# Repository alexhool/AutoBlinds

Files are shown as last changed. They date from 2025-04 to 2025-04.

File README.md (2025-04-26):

# AutoBlinds
### ECE 4180 - Embedded Systems Project

---

## Project Overview

This project automates the opening and closing of roller blinds operated by a beaded chain, enhancing user convenience
and accessibility. The system can be retrofitted to most existing chain operated blinds. It utilizes an ESP32-C6
microcontroller to control a DC motor to open, close, or move the blinds to specific positions. Users can interact with
the system through several methods: **tactile switches** for manual operation, **time-of-flight (ToF) sensor** for
proximity control, and a **web interface** for remote activation and configuring daily activation schedules. The system
operates using a finite state machine with several distinct modes:

* **Toggle Mode:** Default operation mode where pressing the Open/Close buttons or proximity detection via the ToF
sensor move the blinds to their configured positions.

* **Manual Mode:** Activated by a pressing the Mode button, allows for precise position control by holding the
Open/Close buttons. The system automatically returns to Toggle Mode after a set timeout.

* **Configuration Mode:** Activated by holding the Mode button, allows the user to set the fully open and closed
position limits into non-volatile memory by holding the Open/Close buttons. The system automatically returns to Toggle
Mode after a set timeout.

---

## System Components

* **Microcontroller (ESP32-C6-DevKitC-1):** The central processing unit, executing the main control loop and
state machine logic. It manages peripherals via GPIO and I2C, handles networking tasks (Wi-Fi connection, Network Time
Protocol (NTP) synchronization, web interface), reads the encoder with its internal Pulse Counter (PCNT) module, and
controls the motor driver.

* **DC Motor w/ Encoder (JGY-370-EN):** A 158:1 geared DC motor that drives the physical movement of the blinds via the
beaded chain. Its integrated quadrature encoder provides rotational feedback for precise position tracking.
    + **3D-Printed Sprocket:** Mechanically couples the motor shaft to the beaded chain with the correct pitch and
        diameter. Model files available in `assets/`.<br/><br/>
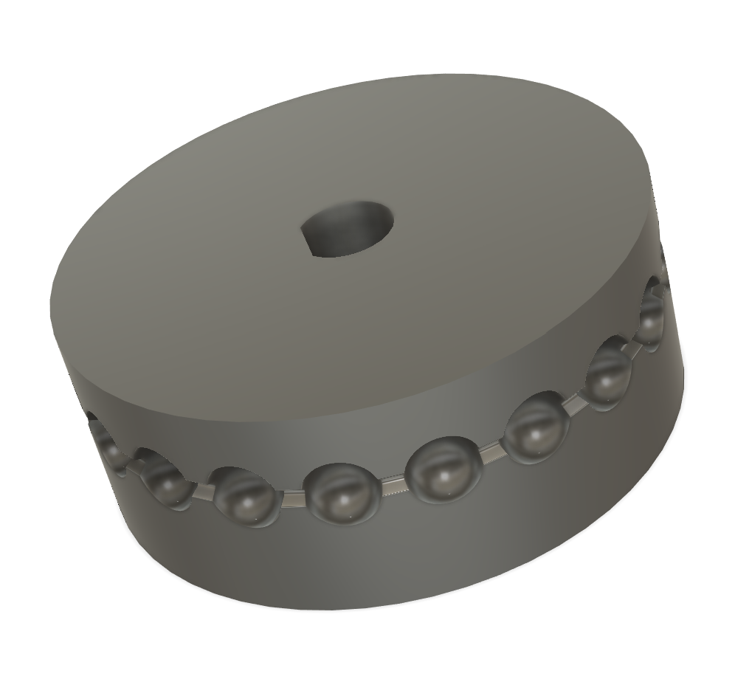
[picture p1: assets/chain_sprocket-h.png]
Chain Sprocket - Horizontal
        
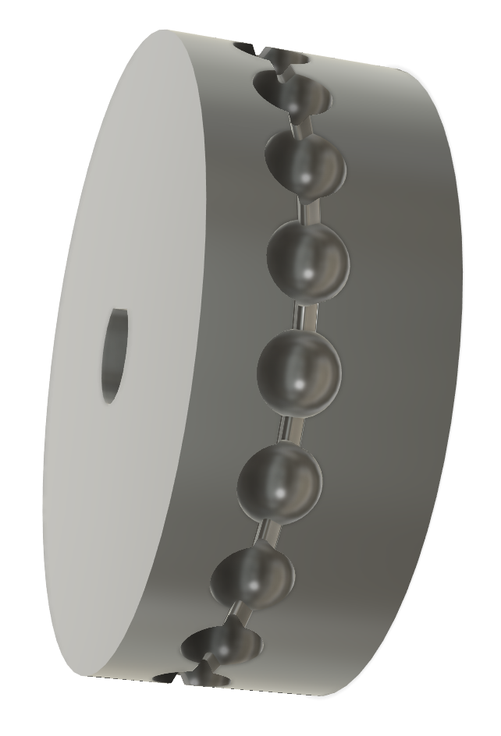
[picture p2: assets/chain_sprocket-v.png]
Chain Sprocket - Vertical
        
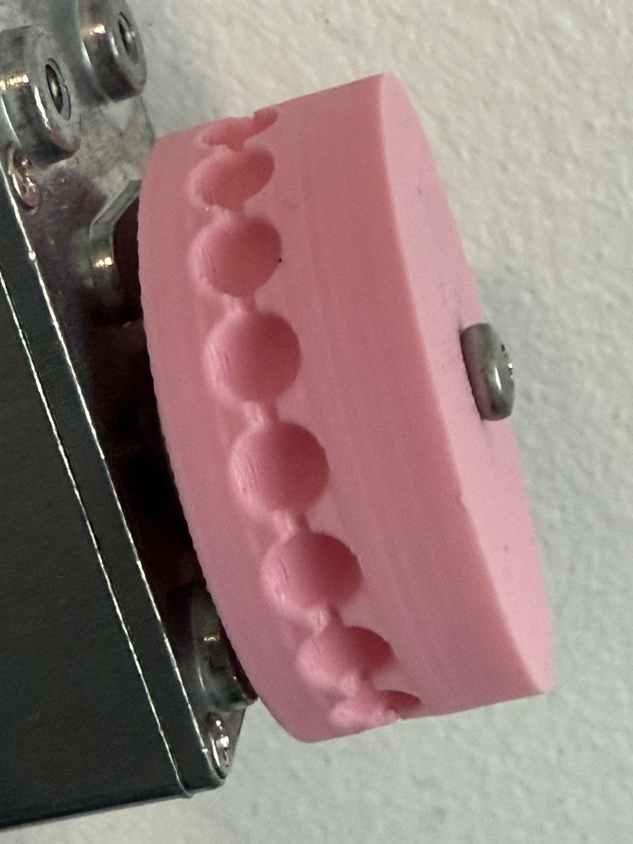
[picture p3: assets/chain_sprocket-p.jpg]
Chain Sprocket - 3D Printed
        
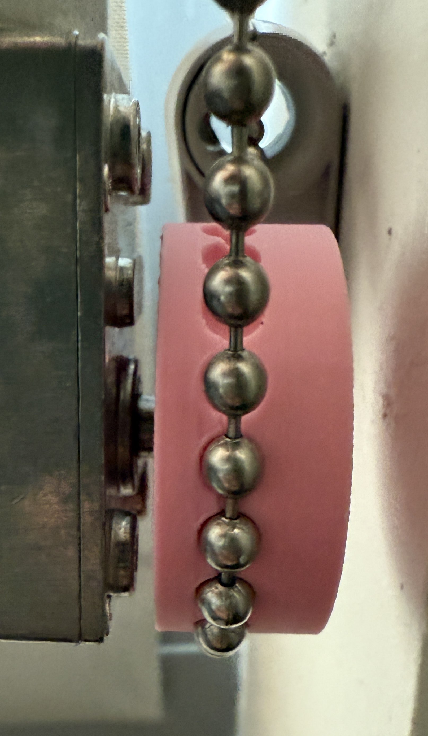
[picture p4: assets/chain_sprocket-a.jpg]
Chain Sprocket - Application
        

* **Motor Driver (TB6612FNG):** An H-bridge to control the DC motor since the ESP32's GPIO pins cannot supply enough
current or voltage to directly power the motor. It receives PWM and direction signals from the ESP32, enabling forward,
reverse, speed control, and braking.

* **Time-of-Flight Sensor (VL53L0X):** An I2C sensor for proximity detection to enable touchless operation. It checks
if a user's hand gesture is within the range threshold, allowing the blinds to toggle between open/closed states or
interrupt current movement.

* **Timekeeping:** It uses the ESP32's internal timer for scheduled remote activation, allowing the blinds to open or
close automatically at user-defined times. Ihe timer periodically synchronized with an NTP server over Wi-FI to prevent
drift.

* **Web Interface:** An asynchronous web server for remote control and configuration over Wi-Fi. Users can open or
close their blinds and program the daily activation schedule without physical access to the device. The schedules are
saved to the ESP32's non-volatile memory.

* **Tactile Switches (SPST):** Three momentary buttons that provide the primary means for manual opening/closing,
switching between operational modes (Toggle, Manual, and Configuration), and setting the physical open/close limits
during the setup process.

* **RGB LED:** It provides visual status feedback to the user, indicating the system's current state (Setup, Idle,
Moving Open, Moving Close, Manual Mode, Config Open, Config Close, Config Save, and Error) and aiding in
troubleshooting.

* **Buck Converter:** It converts the 12V input supply voltage to 5V in order to power the ESP32 and peripherals.

---

## Circuit Diagram

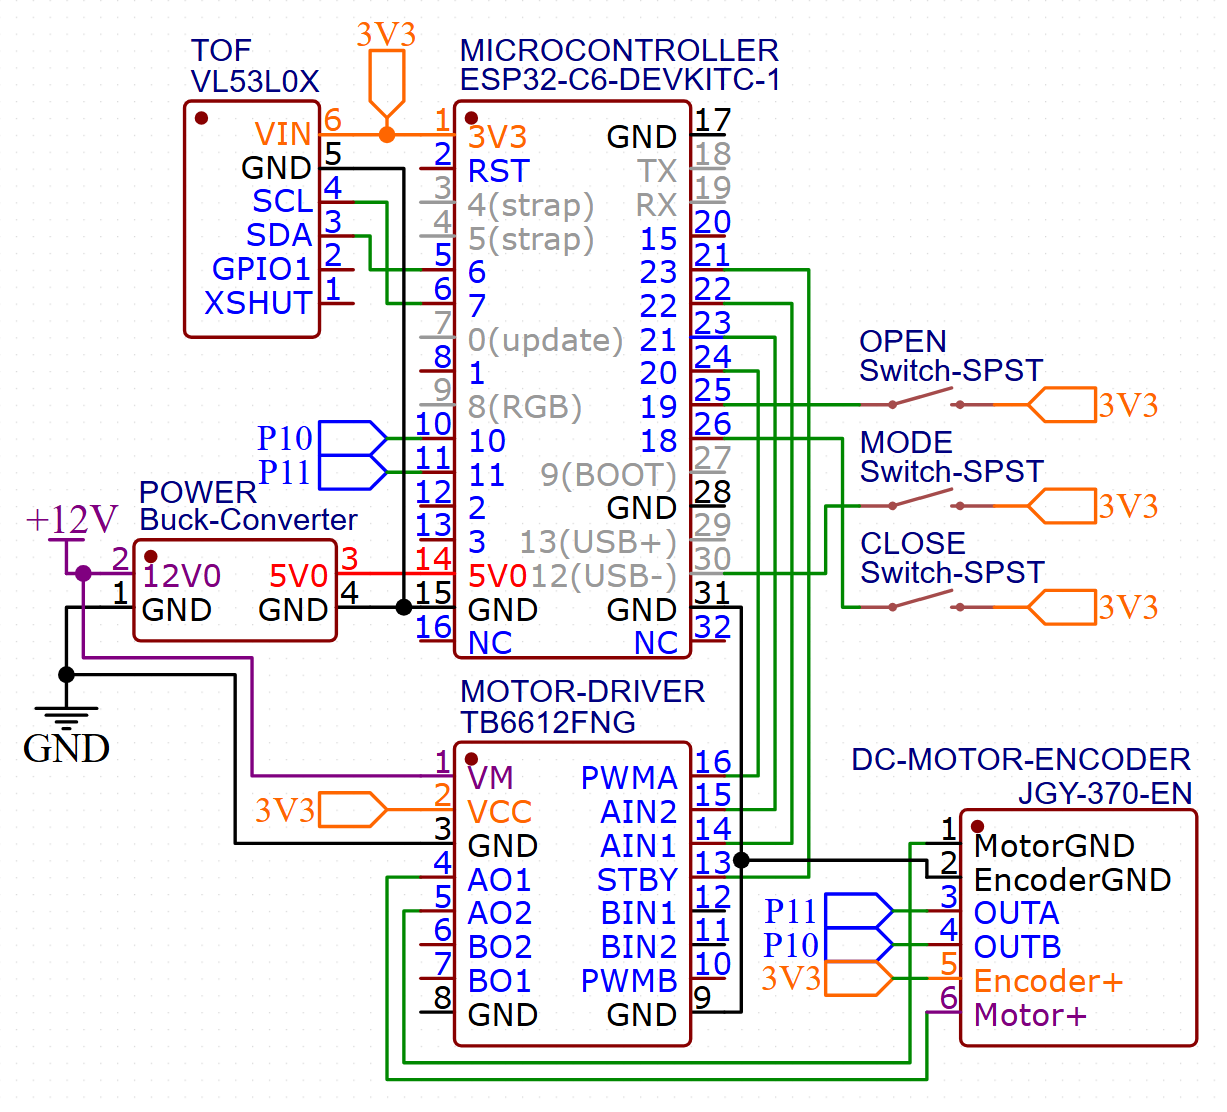
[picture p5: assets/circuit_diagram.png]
Circuit Diagram


---

## Problems Encountered

* **ESP32-C6 Compatibility:** Integrating the ESP32-C6 was challenging due to its novelty. A significant
portion of development time was dedicated to utilizing the encoder as the board has newer PCNT harware. This involved
creating a custom library (`ESP32PCNTEncoder`) by navigating technical documentation and using an existing Arduino
library as a baseline.

* **Position Accuracy:** Maintaining accurate encoder readings during rapid motor movements was challenging due to
motor coasting at the target position. Adjusting the motor driver outputs to enable braking resolved the drift.
Setting an appropriate position tolerance and saving the last known encoder position to memory helped prevent
inaccuracies even after a power loss.

* **State Machine Logic:** Ensuring clean transitions between system states required careful debugging. Initially, the
system occasionally skipped states upon button release. This was resolved by implementing boolean flags to correctly
handle button events during specific state transitions. Managing timeouts for different modes also added complexity.

* **Web Server & Persistence:** Implementing the web server’s scheduler, parsing HTML form data, and reliably saving
settings presented difficulties. Parsing the form required discovering the `sscanf()` function. During debugging, it
became clear that saving schedules was failing because the key names exceeded the maximum length allowed by the
Preferences library.

---

## Comparison to Real-World Systems

* **Target Application:** Unlike products such as SwitchBot Curtain, which are designed for rail-based curtains moving
horizontally, AutoBlinds specifically targets roller blinds operated by a vertical beaded chain.

* **Installation & Cost:** AutoBlinds is a cost-effective retrofit solution for existing beaded chain roller blinds,
whereas many commercial motorized blind systems require a complete replacement of the window covering.

* **Control Methods:** Unlike many commercial options that rely on proprietary RF protocols or cloud services,
AutoBlinds offers local network control via its web interface, enhancing user privacy and eliminating the need for app
downloads. It also supports a wider range of control inputs, improving accessibility and operational independence.

* **Power:** AutoBlinds requires a wired 12V power source, whereas most commercial solutions typically offer
battery-powered options.

---

## Potential Improvements

* **Motor Control:** Implement a PID control loop for smoother, more precise movement, and develop an automatic
calibration routine to detect blind position limits during initial setup.

* **Scheduling:** Implement per-day scheduling options and allow setting schedules based on sunrise and sunset times.

* **User Interface:** Develop a more sophisticated web interface with improved visual design, real-time status updates,
and graphical blind position feedback/control.

* **Security:** Enhance the security of the web interface with basic authentication and HTTPS encryption to prevent
unauthorized access.

* **Over-the-Air (OTA) Updates:** Implement OTA firmware updates via Wi-Fi to eliminate the need for physical access
for reflashing.

* **Enclosure:** Create a 3D-printed enclosure and a custom PCB for the components for a smaller, aesthetically
pleasing package.

* **Power:** Design a version that can be powered by rechargeable batteries, with appropriate power management (sleep
modes, battery monitoring, and interrupts instead of polling).

---

## Dependencies

* **Preferences:**
    + Part of the Arduino Core for ESP32, used for non-volatile storage.
    + License: [LGPL-2.1](https://github.com/espressif/arduino-esp32/blob/master/LICENSE.md)
        ([github.com/espressif/arduino-esp32](https://github.com/espressif/arduino-esp32))

* **ESP32PCNTEncoder (Custom Library):**
    + A derivative of the ESP32Encoder library by hephaestus, used for reading the motor encoder.
    + License: [LGPL-3.0](LICENSE) (`LICENSE`)
    + Base Library:
        - Copyright (C) 2018 hephaestus
        - License: [BSD-like](lib/ESP32PCNTEncoder/LICENSE_ESP32Encoder) (`lib/ESP32PCNTEncoder/LICENSE_ESP32Encoder`)

* **VL53L0X:**
    + Used for ToF sensor interfacing.
    + Copyright:
        - (C) 2017-2022 Pololu Corporation
        - (C) 2016 STMicroelectronics International N.V.
    + License: [MIT+BSD-like](.pio/libdeps/esp32-c6-devkitc-1/VL53L0X/LICENSE.txt) (`.pio/.../VL53L0X/LICENSE.txt`)

* **WiFiManager:**
    + Used for Wi-Fi configuration.
    + Copyright (C) 2015 tzapu
    + License: [MIT](.pio/libdeps/esp32-c6-devkitc-1/WiFiManager/LICENSE) (`.pio/.../WiFiManager/LICENSE`)

* **AsyncTCP:**
    + Used for asynchronous TCP communication.
    + Copyright (C) 2016-2025 Hristo Gochkov, Mathieu Carbou, Emil Muratov
    + License: [LGPL-3.0](.pio/libdeps/esp32-c6-devkitc-1/AsyncTCP/LICENSE) (`.pio/.../AsyncTCP/LICENSE`)

* **ESPAsyncWebServer:**
    + Used for running the asynchronous web server.
    + Copyright (C) 2016-2025 Hristo Gochkov, Mathieu Carbou, Emil Muratov
    + License: [LGPL-3.0](.pio/libdeps/esp32-c6-devkitc-1/ESPAsyncWebServer/LICENSE)
        (`.pio/.../ESPAsyncWebServer/LICENSE`)

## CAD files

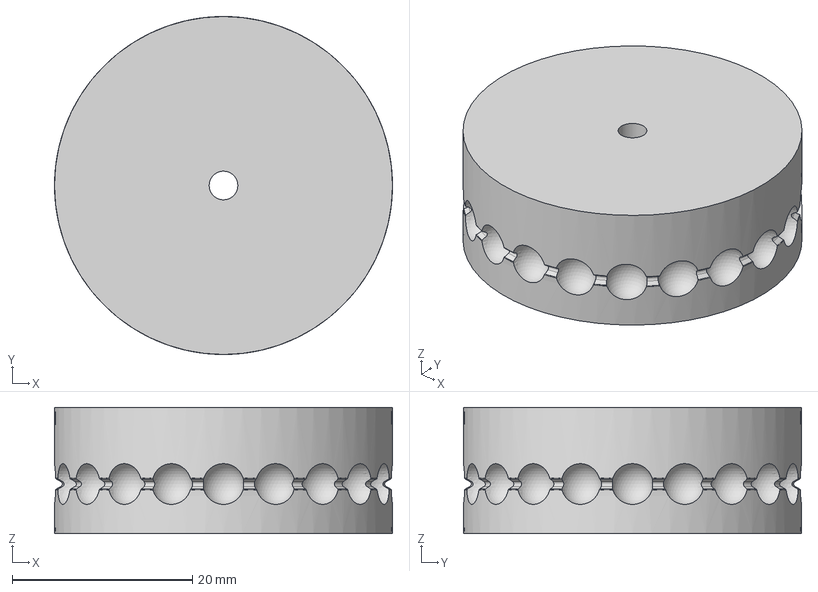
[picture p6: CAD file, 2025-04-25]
assets/chain_sprocket.step
37.5 x 37.5 x 14.0 mm

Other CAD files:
assets/chain_sprocket.f3d
assets/chain_sprocket.stl

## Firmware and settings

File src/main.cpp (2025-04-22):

/*
 * SPDX-License-Identifier: LGPL-3.0-or-later
 * SPDX-FileCopyrightText: Copyright 2025 Alexander Hool
 */

#include <Arduino.h>
#include "memory.h"
#include "buttons.h"
#include "motor.h"
#include "tof.h"
#include "states.h"
#include "schedule.h"

void setup() {
  // Sold blue
  rgbLedWrite(RGB_BUILTIN, 0, 0, 255);
  Serial.begin(115200);
  Serial.print("\n--- Setup ---\n");

  // Initialize external components
  if (!setupMemory() || !setupMotor() || !setupTof()) {
    Serial.print("ERROR: Initialization Failed\n");
    while (true) {
      // Blink red on error
      if ((millis() % 1200) < 800) {
        rgbLedWrite(RGB_BUILTIN, 255, 0, 0);
      } else {
        rgbLedWrite(RGB_BUILTIN, 0, 0, 0);
      }
      delay(2);
    }
  }
  if (!setupScheduler()) {
    Serial.print("WARNING: Network Setup Failed - Offline Mode\n");
  }

  // Initialze internal components
  setupButtons();
  setupStates();

  Serial.printf("\n--- Loop ---\n");
}

void loop() {
  unsigned long currentTime = millis();

  // Continuously update system state machine
  updateStateMachine();

  // Periodically resync RTC
  syncRTC();

  // Periodically check schedule
  checkSchedule();

  delay(2);
}

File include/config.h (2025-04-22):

/*
 * SPDX-License-Identifier: LGPL-3.0-or-later
 * SPDX-FileCopyrightText: Copyright 2025 Alexander Hool
 */

#ifndef CONFIG_H
#define CONFIG_H

#include <cstdint>

// Scheduler constants
constexpr uint16_t WEB_SERVER_PORT = 80;
constexpr char WIFI_AP_NAME[] = "AutoBlinds";
constexpr char NTP_SERVER[] = "pool.ntp.org";
constexpr char TIME_ZONE[] = "EST5EDT,M3.2.0/2,M11.1.0/2";
constexpr unsigned long NTP_SYNC_INTERVAL = 12 * 3600 * 1000;
constexpr unsigned long WIFI_CHECK_INTERVAL = 15000;
constexpr unsigned long SCHEDULE_CHECK_INTERVAL = 30000;

// System constants
constexpr uint32_t BTN_DEBOUNCE = 50;
constexpr uint32_t CONFIG_HOLD_TIME = 2000;
constexpr uint32_t MANUAL_TIMEOUT = 15000;
constexpr uint32_t CONFIG_TIMEOUT = 30000;

constexpr int MOTOR_DEFAULT_SPEED = 150;
constexpr int MOTOR_CONFIG_SPEED = 75;
constexpr int64_t POS_TOLERANCE = 42;

constexpr uint16_t TOF_THRESHOLD = 25;
constexpr uint32_t TOF_DEBOUNCE = 400;

// Pin definitions
constexpr uint8_t PIN_BTN_OPEN = 19;
constexpr uint8_t PIN_BTN_MODE = 12;
constexpr uint8_t PIN_BTN_CLOSE = 18;

constexpr uint8_t PIN_MTR_IN1 = 22;
constexpr uint8_t PIN_MTR_IN2 = 21;
constexpr uint8_t PIN_MTR_PWM = 20;
constexpr uint8_t PIN_MTR_STBY = 23;
constexpr uint8_t PIN_ENC_A = 11;
constexpr uint8_t PIN_ENC_B = 10;
constexpr uint8_t ENC_PCNT = 0;

constexpr uint8_t PIN_I2C_SDA = 6;
constexpr uint8_t PIN_I2C_SCL = 7;

#endif // CONFIG_H

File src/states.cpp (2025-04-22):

/*
 * SPDX-License-Identifier: LGPL-3.0-or-later
 * SPDX-FileCopyrightText: Copyright 2025 Alexander Hool
 */

#include "states.h"
#include <Arduino.h>
#include <ESP32PCNTEncoder.h>
#include "config.h"
#include "memory.h"
#include "buttons.h"
#include "motor.h"
#include "tof.h"

// RGB LED color definitions
#define RGB_RED 255, 0, 0
#define RGB_GREEN 0, 255, 0
#define RGB_YELLOW 255, 255, 0
#define RGB_CYAN 0, 255, 255
#define RGB_OFF 0, 0, 0

// LED status states
enum LEDStatus {
  STATUS_TOGGLE_IDLE,   // Default
  STATUS_TOGGLE_OPEN,
  STATUS_TOGGLE_CLOSE,
  STATUS_MANUAL,
  STATUS_CONFIG_OPEN,
  STATUS_CONFIG_CLOSE,
  STATUS_CONFIG_SAVE,
  STATUS_ERROR
};

// Get global encoder object from motor.h
extern ESP32PCNTEncoder encoder;

// State machine variables
static SystemState currentState = SystemState::TOGGLE_IDLE;
static SystemState previousState = SystemState::TOGGLE_IDLE;

// Position control variables
static int64_t openPos = 0;
static int64_t closePos = 0;
static int64_t targetPos = 0;
static int64_t tempOpenPos = 0;
static int64_t tempClosePos = 0;
static unsigned long lastActivityTime = 0;

// Button state variables
static bool ignoreOpenRelease = false;
static bool ignoreCloseRelease = false;
static bool ignoreModeManualRelease = false;
static bool ignoreModeConfigRelease = false;
static bool ignoreModeExitRelease = false;

// LED control variables
static LEDStatus currentLEDStatus = STATUS_TOGGLE_IDLE;
static unsigned long statusStartTime = 0;

// Forward declarations
static void startMovingTo(int64_t newTarget);
static void handleToggleModeIdle();
static void handleToggleModeMoving();
static void handleManualMode();
static void handleConfigSetting();
static void handleConfigModeSaving();
static void updateLedIndicator(SystemState systemState);

// Initialize state machine to initial values
void setupStates() {
  Serial.print("Initializing States...");

  loadPositions(openPos, closePos);
  int64_t lastPos = loadLastPosition();
  encoder.setPosition(lastPos);

  enterState(SystemState::TOGGLE_IDLE);

  Serial.print("Done\n");
  Serial.printf("*Loaded Positions: Open = %lld, Close = %lld, Current = %lld\n", openPos, closePos, lastPos);
}

// Handle system state transitions and logic
void updateStateMachine() {
  // Fetch new button states
  updateButtonStates();

  // Execute state-specific logic
  switch (currentState) {
    case SystemState::TOGGLE_IDLE:
      handleToggleModeIdle();
      break;
    case SystemState::TOGGLE_OPEN:
    case SystemState::TOGGLE_CLOSE:
      handleToggleModeMoving();
      break;
    case SystemState::MANUAL_IDLE:
    case SystemState::MANUAL_MOVE:
      handleManualMode();
      break;
    case SystemState::CONFIG_OPEN:
    case SystemState::CONFIG_CLOSE:
      handleConfigSetting();
      break;
    case SystemState::CONFIG_SAVE:
      handleConfigModeSaving();
      break;
    case SystemState::ERROR:
      break;
    default:
      Serial.printf("ERROR: Updated Invalid State: %d\n", (int)currentState);
      enterState(SystemState::ERROR);
      break;
  }

  // Update LED based on current state after handling
  updateLedIndicator(currentState);
}

// Transition to a new state and update LED
void enterState(SystemState newState) {
  if (newState != currentState) {
    Serial.printf("State Change: %d -> %d\n", (int)currentState, (int)newState);
    previousState = currentState;
    currentState = newState;
    lastActivityTime = millis();

    // Execute state-specific logic
    switch (newState) {
      case SystemState::TOGGLE_IDLE:
      case SystemState::MANUAL_IDLE:
        // Save last position for power loss recovery
        saveLastPosition(encoder.getPosition());
        motorStop();
        break;
      case SystemState::TOGGLE_OPEN:
      case SystemState::TOGGLE_CLOSE:
      case SystemState::MANUAL_MOVE:
        break;
      case SystemState::CONFIG_OPEN:
        motorStop();
        Serial.print("Set OPEN Limit\n");
        tempOpenPos = 0;
        tempClosePos = 0;
        ignoreModeConfigRelease = true;
        ignoreModeExitRelease = false;
        break;
      case SystemState::CONFIG_CLOSE:
        motorStop();
        Serial.print("Set CLOSE Limit\n");
        break;
      case SystemState::CONFIG_SAVE:
        motorStop();
        break;
      case SystemState::ERROR:
        motorStop();
        break;
      default:
        motorStop();
        Serial.printf("ERROR: Entered Invalid State: %d\n", (int)newState);
        enterState(SystemState::ERROR);
        break;
    }

    // Update LED indicator based on new state
    updateLedIndicator(newState);
  }
}

// Move to open position from external trigger
void triggerOpen() {
  if (currentState == SystemState::TOGGLE_IDLE) {
    startMovingTo(openPos);
  }
}

// Move to close position from external trigger
void triggerClose() {
  if (currentState == SystemState::TOGGLE_IDLE) {
    startMovingTo(closePos);
  }
}

// Move motor to new target position
static void startMovingTo(int64_t newTarget) {
  int64_t currentPos = encoder.getPosition();
  int motorSpeed = 0;
  SystemState nextState = currentState;
  targetPos = newTarget;

  // Check if already at target
  if (abs(currentPos - targetPos) <= POS_TOLERANCE) {
    Serial.print("Already at Target Position\n");
    if (currentState == SystemState::TOGGLE_OPEN || currentState == SystemState::TOGGLE_CLOSE) {
      enterState(SystemState::TOGGLE_IDLE);
    }
    return;
  }

  // Determine motor direction
  motorSpeed = (targetPos > currentPos) ? MOTOR_DEFAULT_SPEED : -MOTOR_DEFAULT_SPEED;

  // Determine next state based on target position
  if (currentState == SystemState::TOGGLE_IDLE) {
    if (newTarget == openPos) {
      nextState = SystemState::TOGGLE_OPEN;
    } else if (newTarget == closePos) {
      nextState = SystemState::TOGGLE_CLOSE;
    } else {
      Serial.printf("ERROR: Attempted Move with Invalid Target: %lld\n", newTarget);
      enterState(SystemState::ERROR);
      return;
    }
  } else {
    Serial.printf("ERROR: Attempted Move from Unexpected State: %d\n", (int)currentState);
    enterState(SystemState::ERROR);
  }

  // Move motor
  Serial.printf("Moving to %lld (Current: %lld)\n", targetPos, currentPos);
  motorMove(motorSpeed);
  if (nextState != currentState) {
    enterState(nextState);
  }
  lastActivityTime = millis();
}
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

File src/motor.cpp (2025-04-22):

/*
 * SPDX-License-Identifier: LGPL-3.0-or-later
 * SPDX-FileCopyrightText: Copyright 2025 Alexander Hool
 */

#include "motor.h"
#include <Arduino.h>
#include <ESP32PCNTEncoder.h>
#include "config.h"

// Define global encoder object
ESP32PCNTEncoder encoder(PIN_ENC_A, PIN_ENC_B, ENC_PCNT);

// Initialize motor driver GPIO and encoder
bool setupMotor() {
  Serial.print("Initializing Motor...");

  // Set motor driver pins as outputs
  pinMode(PIN_MTR_IN1, OUTPUT);
  pinMode(PIN_MTR_IN2, OUTPUT);
  pinMode(PIN_MTR_PWM, OUTPUT);
  pinMode(PIN_MTR_STBY, OUTPUT);
  digitalWrite(PIN_MTR_STBY, HIGH);
  motorStop();

  // Set glitch filter time to ignore noise (ns)
  encoder.setFilterNs(10000);
  // Set encoder type to full quadrature (4 PPR)
  encoder.setEncoderType(EncoderType::FULL_QUAD);
  // Attempt to start encoder counting
  uint8_t attempts = 10;
  while (!encoder.begin() && attempts > 0) {
    attempts--;
    Serial.print(".");
    delay(500);
  }
  if (attempts == 0) {
    Serial.print("Failed\n");
    return false;
  }
  // Start count from 0
  encoder.resetPosition();

  Serial.print("Done\n");
  return true;
}

// Move the motor at a given speed (-255 to 255)
void motorMove(int speed) {
  // Stop motor if speed is 0
  if (speed == 0) {
    motorStop();
    return;
  }

  // Determine direction and set PWM
  if (speed > 0) {
    // Clockwise rotation
    digitalWrite(PIN_MTR_IN1, HIGH);
    digitalWrite(PIN_MTR_IN2, LOW);
    analogWrite(PIN_MTR_PWM, constrain(speed, 0, 255));
  } else {
    // Counterclockwise rotation
    digitalWrite(PIN_MTR_IN1, LOW);
    digitalWrite(PIN_MTR_IN2, HIGH);
    analogWrite(PIN_MTR_PWM, constrain(abs(speed), 0, 255));
  }
}

// Stop motor rotation
void motorStop() {
  // Set IN pins to HIGH for brake mode
  digitalWrite(PIN_MTR_IN1, HIGH);
  digitalWrite(PIN_MTR_IN2, HIGH);
  analogWrite(PIN_MTR_PWM, 0);
}

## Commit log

2025-04-12 nonworking encoder
2025-04-12 working encoder
2025-04-12 organize encoder lib files
2025-04-13 add encoder types
2025-04-13 reconfigure encoder types
2025-04-14 rename esp32encoder license
2025-04-19 add interface for motor control
2025-04-19 fix tof debounce logic
    [tof.cpp]
2025-04-19 add interface for button handling
2025-04-19 fix setup print formatting
    [buttons.cpp, motor.cpp]
2025-04-19 encapsulate ButtonState enum
2025-04-19 move memory prints externally
2025-04-20 switch to active braking instead of coasting
2025-04-20 print exact trigger distance
2025-04-20 squash state transition bugs
    [config.h, states.cpp]
2025-04-20 print formats
2025-04-20 mode toggle interrupts toggle movement
2025-04-20 more robust error handling
    [buttons.cpp, config.h, main.cpp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]
2025-04-21 save encoder position for power loss recovery
2025-04-21 fix missing error state transition
    [schedule.cpp, states.cpp]
2025-04-22 fix rtc time sync
    [config.h, schedule.cpp]
2025-04-22 fix saving schedules to memory
    [main.cpp, memory.cpp, schedule.cpp]
2025-04-22 proper print formatting
2025-04-25 add assets
    [chain_sprocket.f3d, chain_sprocket.step, chain_sprocket.stl]
2025-04-26 update README w/ circuit diagram
